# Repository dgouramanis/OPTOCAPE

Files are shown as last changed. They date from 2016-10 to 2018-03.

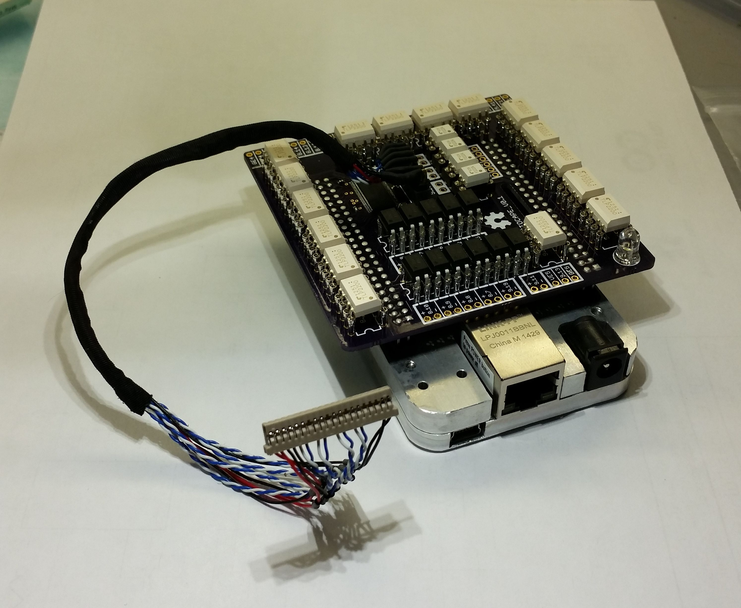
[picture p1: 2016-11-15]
hardware/images/optocape_lvds_cable.jpeg

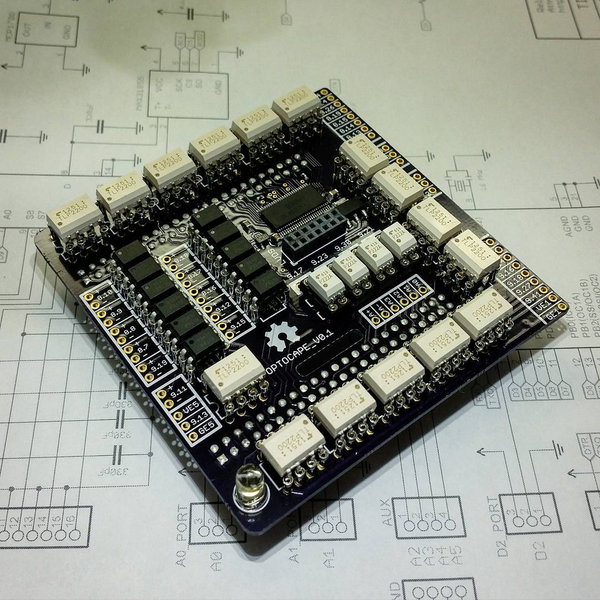
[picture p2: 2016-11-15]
hardware/images/optocape_top.png

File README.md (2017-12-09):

Photocoupler cape for BeagleBone Black with integrated video serializer

https://youtu.be/7uQYPXgA6WU

This cape was originally designed for a CNC milling machine. The opto-I/O was designed to accomidate four stepper axis with limit switches, spindle, coolant, LED light, and more. 

The UI section of the cape includes a LVDS serializer compatible with many flatscreen LCDs. Four-wire touchscreen is supported.

Features:

    15 high-speed outputs (opto)
    10 high-speed inputs (opto)
    UART TX RX (opto)    
    4 opto relay outputs (500mA)
    12 bit color LVDS video (CMOS)
    4 analog inputs (CMOS)

The outputs are divided into five sections. Each section is powered through seperate V and GND nets. 

The input voltage range is 3-6 volts.

5 VDC power source connected to DC power Jack or VDD_5V is required for LVDS.

You can buy an Optocape at the link below. 

https://www.tindie.com/products/TEMProducts/optocape/

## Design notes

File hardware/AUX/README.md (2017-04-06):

This auxiliary circuit is for connection of a mechanical switch panl user interface via UART4. Not yet tested.

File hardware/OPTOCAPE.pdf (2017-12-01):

TEM Products | Optocape

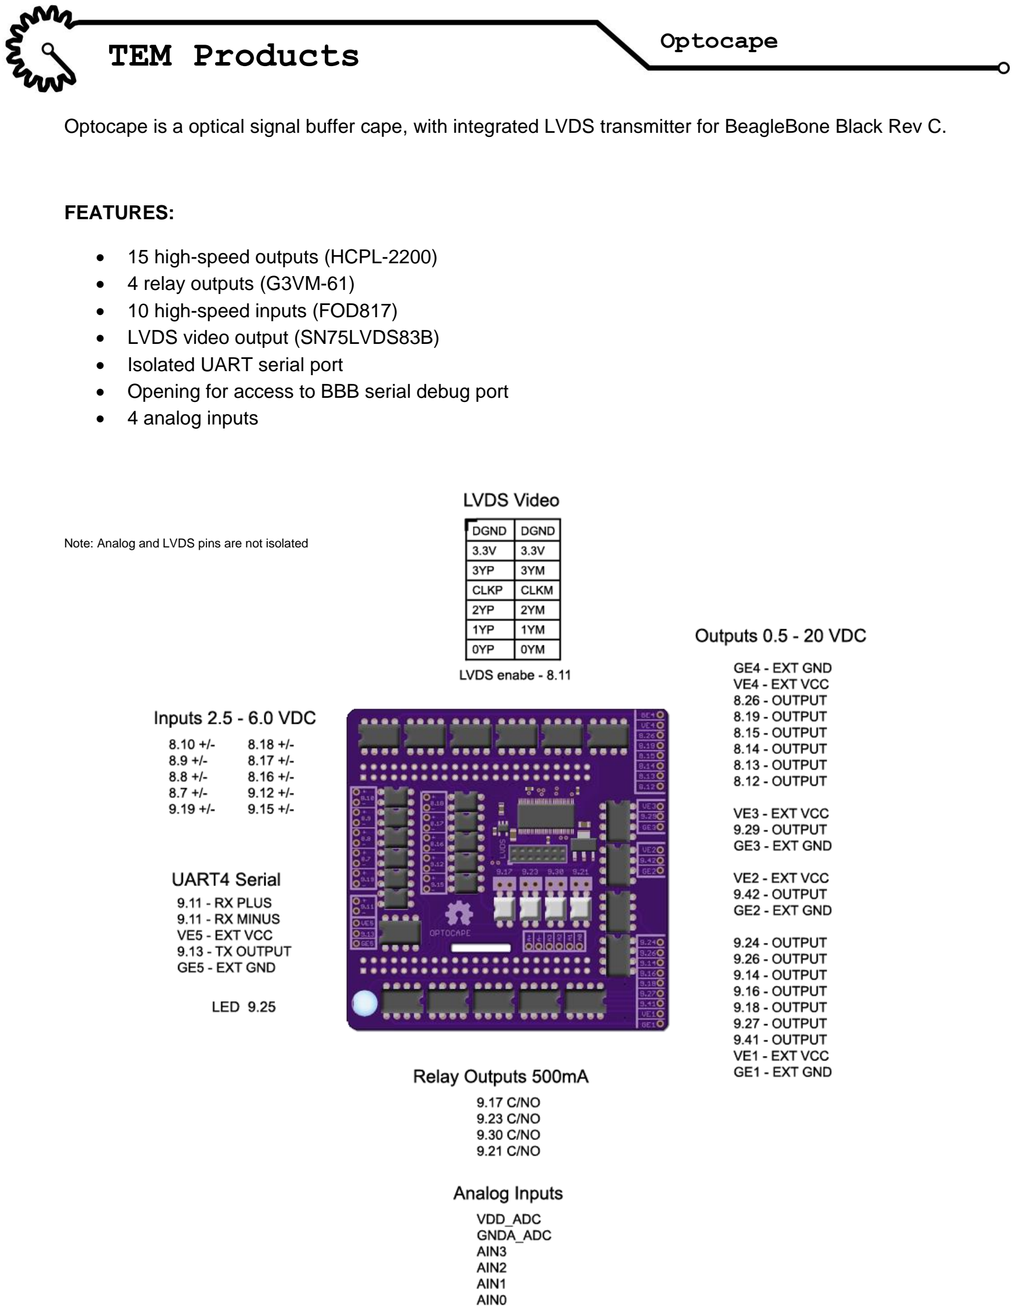
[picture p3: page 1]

Optocape is a optical signal buffer cape, with integrated LVDS transmitter for BeagleBone Black Rev C.

FEATURES:

- 15 high-speed outputs (HCPL-2200)
- 4 relay outputs (G3VM-61)
- 10 high-speed inputs (FOD817)
- LVDS video output (SN75LVDS83B)
- Isolated UART serial port
- Opening for access to BBB serial debug port
- 4 analog inputs

Note: Analog and LVDS pins are not isolated

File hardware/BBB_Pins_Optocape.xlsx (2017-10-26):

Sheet: P8
Optocape I/O | Pin | ZCZ Ball | Name | DT Offset | Mode
 |  |  |  |  | 0 | 1 | 2 | 3 | 4 | 5 | 6 | 7
 | 1 | - | GND
 | 2 | - | GND
 | 3 | R9 | GPIO1_6 | 0x018 | gpmc_ad6 | mmc1_dat6 | - | - | - | - | - | gpio1[6]
 | 4 | T9 | GPIO1_7 | 0x01C | gpmc_ad7 | mmc1_dat7 | - | - | - | - | - | gpio1[7]
 | 5 | R8 | GPIO1_2 | 0x008 | gpmc_ad2 | mmc1_dat2 | - | - | - | - | - | gpio1[2]
 | 6 | T8 | GPIO1_3 | 0x00C | gpmc_ad3 | mmc1_dat3 | - | - | - | - | - | gpio1[3]
I | 7 | R7 | TIMER4 | 0x090 | gpmc_advn_ale | - | timer4 | - | - | - | - | gpio2[2]
I | 8 | T7 | TIMER7 | 0x094 | gpmc_oen_ren | - | timer7 | - | - | - | - | gpio2[3]
I | 9 | T6 | TIMER5 | 0x09C | gpmc_ben0_cle | - | timer5 | - | - | - | - | gpio2[5]
I | 10 | U6 | TIMER6 | 0x098 | gpmc_wen | - | timer6 | - | - | - | - | gpio2[4]
LVDS ena | 11 | R12 | GPIO1_13 | 0x034 | gpmc_ad13 | lcd_data18 | mmc1_dat5 | mmc2_dat1 | eQEP2B_in | pr1_mii0_txd1 | pr1_pru0_pru_r30_15 | gpio1[13]
O | 12 | T12 | GPIO1_12 | 0x030 | gpmc_ad12 | lcd_data19 | mmc1_dat4 | mmc2_dat0 | eQEP2A_IN | pr1_mii0_txd2 | pr1_pru0_pru_r30_14 | gpio1[12]
O | 13 | T10 | EHRPWM2B | 0x024 | gpmc_ad9 | lcd_data22 | mmc1_dat1 | mmc2_dat5 | ehrpwm2B | pr1_mii0_col | - | gpio0[23]
O | 14 | T11 | GPIO0_26 | 0x028 | gpmc_ad10 | lcd_data21 | mmc1_dat2 | mmc2_dat6 | ehrpwm2_tripzone_in | pr1_mii0_txen | - | gpio0[26]
O | 15 | U13 | GPIO1_15 | 0x03C | gpmc_ad15 | lcd_data16 | mmc1_dat7 | mmc2_dat3 | eQEP2_strobe | pr1_ecap0_ecap_capin_apwm_o | pr1_pru0_pru_r31_15 | gpio1[15]
I | 16 | V13 | GPIO1_14 | 0x038 | gpmc_ad14 | lcd_data17 | mmc1_dat6 | mmc2_dat2 | eQEP2_index | pr1_mii0_txd0 | pr1_pru0_pru_r31_14 | gpio1[14]
I | 17 | U12 | GPIO0_27 | 0x02C | gpmc_ad11 | lcd_data20 | mmc1_dat3 | mmc2_dat7 | ehrpwm0_synco | pr1_mii0_txd3 | - | gpio0[27]
I | 18 | V12 | GPIO2_1 | 0x08C | gpmc_clk | lcd_memory_clk | gpmc_wait1 | mmc2_clk | pr1_mii1_crs | pr1_mdio_mdclk | mcasp0_fsr | gpio2[1]
O | 19 | U10 | EHRPWM2A | 0x020 | gpmc_ad8 | lcd_data23 | mmc1_dat0 | mmc2_dat4 | ehrpwm2A | pr1_mii_mt0_clk | - | gpio0[22]
 | 20 | V9 | GPIO1_31 | 0x084 | gpmc_csn2 | gpmc_be1n | mmc1_cmd | pr1_edio_data_in7 | pr1_edio_data_out7 | pr1_pru1_pru_r30_13 | pr1_pru1_pru_r31_13 | gpio1[31]
 | 21 | U9 | GPIO1_30 | 0x080 | gpmc_csn1 | gpmc_clk | mmc1_clk | pr1_edio_data_in6 | pr1_edio_data_out6 | pr1_pru1_pru_r30_12 | pr1_pru1_pru_r31_12 | gpio1[30] | Output
 | 22 | V8 | GPIO1_5 | 0x014 | gpmc_ad5 | mmc1_dat5 | - | - | - | - | - | gpio1[5] | Input
 | 23 | U8 | GPIO1_4 | 0x010 | gpmc_ad4 | mmc1_dat4 | - | - | - | - | - | gpio1[4] | I/O
 | 24 | V7 | GPIO1_1 | 0x004 | gpmc_ad1 | mmc1_dat1 | - | - | - | - | - | gpio1[1]
 | 25 | U7 | GPIO1_0 | 0x000 | gpmc_ad0 | mmc1_dat0 | - | - | - | - | - | gpio1[0]
O | 26 | V6 | GPIO1_29 | 0x07C | gpmc_csn0 | - | - | - | - | - | - | gpio1[29]
 | 27 | U5 | GPIO2_22 | 0x0E0 | lcd_vsync | gpmc_a8 | gpmc_a1 | pr1_edio_data_in2 | pr1_edio_data_out2 | pr1_pru1_pru_r30_8 | pr1_pru1_pru_r31_8 | gpio2[22]
 | 28 | V5 | GPIO2_24 | 0x0E8 | lcd_pclk | gpmc_a10 | pr1_mii0_crs | pr1_edio_data_in4 | pr1_edio_data_out4 | pr1_pru1_pru_r30_10 | pr1_pru1_pru_r31_10 | gpio2[24]
 | 29 | R5 | GPIO2_23 | 0x0E4 | lcd_hsync | gpmc_a9 | gpmc_a2 | pr1_edio_data_in3 | pr1_edio_data_out3 | pr1_pru1_pru_r30_9 | pr1_pru1_pru_r31_9 | gpio2[23]
 | 30 | R6 | GPIO2_25 | 0x0EC | lcd_ac_bias_en | gpmc_a11 | pr1_mii1_crs | pr1_edio_data_in5 | pr1_edio_data_out5 | pr1_pru1_pru_r30_11 | pr1_pru1_pru_r31_11 | gpio2[25]
 | 31 | V4 | UART5_CTSN | 0x0D8 | lcd_data14 | gpmc_a18 | eQEP1_index | mcasp0_axr1 | uart5_rxd | pr1_mii0_rxd3 | uart5_ctsn | gpio0[10]
 | 32 | T5 | UART5_RTSN | 0x0DC | lcd_data15 | gpmc_a19 | eQEP1_strobe | mcasp0_ahclkx | mcasp0_axr3 | pr1_mii0_rxdv | uart5_rtsn | gpio0[11]
 | 33 | V3 | UART4_RTSN | 0x0D4 | lcd_data13 | gpmc_a17 | eQEP1B_in | mcasp0_fsr | mcasp0_axr3 | pr1_mii0_rxer | uart4_rtsn | gpio0[9]
 | 34 | U4 | UART3_RTSN | 0x0CC | lcd_data11 | gpmc_a15 | ehrpwm1B | mcasp0_ahclkr | mcasp0_axr2 | pr1_mii0_rxd0 | uart3_rtsn | gpio2[17]
 | 35 | V2 | UART4_CTSN | 0x0D0 | lcd_data12 | gpmc_a16 | eQEP1A_in | mcasp0_aclkr | mcasp0_axr2 | pr1_mii0_rxlink | uart4_ctsn | gpio0[8]
 | 36 | U3 | UART3_CTSN | 0x0C8 | lcd_data10 | gpmc_a14 | ehrpwm1A | mcasp0_axr0 | - | pr1_mii0_rxd1 | uart3_ctsn | gpio2[16]
 | 37 | U1 | UART5_TXD | 0x0C0 | lcd_data8 | gpmc_a12 | ehrpwm1_tripzone_in | mcasp0_aclkx | uart5_txd | pr1_mii0_rxd3 | uart2_ctsn | gpio2[14]
 | 38 | U2 | UART5_RXD | 0x0C4 | lcd_data9 | gpmc_a13 | ehrpwm0_synco | mcasp0_fsx | uart5_rxd | pr1_mii0_rxd2 | uart2_rtsn | gpio2[15]
 | 39 | T3 | GPIO2_12 | 0x0B8 | lcd_data6 | gpmc_a6 | pr1_edio_data_in6 | eQEP2_index | pr1_edio_data_out6 | pr1_pru1_pru_r30_6 | pr1_pru1_pru_r31_6 | gpio2[12]
 | 40 | T4 | GPIO2_13 | 0x0BC | lcd_data7 | gpmc_a7 | pr1_edio_data_in7 | eQEP2_strobe | pr1_edio_data_out7 | pr1_pru1_pru_r30_7 | pr1_pru1_pru_r31_7 | gpio2[13]
 | 41 | T1 | GPIO2_10 | 0x0B0 | lcd_data4 | gpmc_a4 | pr1_mii0_txd1 | eQEP2A_in | - | pr1_pru1_pru_r30_4 | pr1_pru1_pru_r31_4 | gpio2[10]
 | 42 | T2 | GPIO2_11 | 0x0B4 | lcd_data5 | gpmc_a5 | pr1_mii0_txd0 | eQEP2B_in | - | pr1_pru1_pru_r30_5 | pr1_pru1_pru_r31_5 | gpio2[11]
 | 43 | R3 | GPIO2_8 | 0x0A8 | lcd_data2 | gpmc_a2 | pr1_mii0_txd3 | ehrpwm2_tripzone_in | - | pr1_pru1_pru_r30_2 | pr1_pru1_pru_r31_2 | gpio2[8]
 | 44 | R4 | GPIO2_9 | 0x0AC | lcd_data3 | gpmc_a3 | pr1_mii0_txd2 | ehrpwm0_synco | - | pr1_pru1_pru_r30_3 | pr1_pru1_pru_r31_3 | gpio2[9]
 | 45 | R1 | GPIO2_6 | 0x0A0 | lcd_data0 | gpmc_a0 | pr1_mii_mt0_clk | ehrpwm2A | - | pr1_pru1_pru_r30_0 | pr1_pru1_pru_r31_0 | gpio2[6]
 | 46 | R2 | GPIO2_7 | 0x0A4 | lcd_data1 | gpmc_a1 | pr1_mii0_txen | ehrpwm2B | - | pr1_pru1_pru_r30_1 | pr1_pru1_pru_r31_1 | gpio2[7]

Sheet: P9
Optocape I/O | Pin | ZCZ Ball | Name | DT Offset | Mode
 |  |  |  |  | 0 | 1 | 2 | 3 | 4 | 5 | 6 | 7
 | 1 | - | GND
 | 2 | - | GND
 | 3 | - | DC_3.3V
 | 4 | - | DC_3.3V
 | 5 | - | VDD_5V
 | 6 | - | VDD_5V
 | 7 | - | SYS_5V
 | 8 | - | SYS_5V
 | 9 | - | PWR_BUT
 | 10 | A10 | SYS_RESETn |  | RESET_OUT | - | - | - | - | - | - | -
I | 11 | T17 | UART4_RXD | 0x070 | gpmc_wait0 | mii2_crs | gpmc_csn4 | rmii2_crs_dv | mmc1_sdcd | pr1_mii1_col | uart4_rxd | gpio0[30]
I | 12 | U18 | GPIO1_28 | 0x078 | gpmc_ben1 | mii2_col | gpmc_csn6 | mmc2_dat3 | gpmc_dir | pr1_mii1_rxlink | mcasp0_aclkr | gpio1[28]
O | 13 | U17 | UART4_TXD | 0x074 | gpmc_wpn | mii2_rxerr | gpmc_csn5 | rmii2_rxerr | mmc2_sdcd | pr1_mii1_txen | uart4_txd | gpio0[31]
O | 14 | U14 | EHRPWM1A | 0x048 | gpmc_a2 | mii2_txd3 | rgmii2_td3 | mmc2_dat1 | gpmc_a18 | pr1_mii1_txd2 | ehrpwm1A | gpio1[18]
I | 15 | R13 | GPIO1_16 | 0x040 | gpmc_a0 | gmii2_txen | rmii2_tctl | mii2_txen | gpmc_a16 | pr1_mii_mt1_clk | ehrpwm1_tripzone_input | gpio1[16]
O | 16 | T14 | EHRPWM1B | 0x04C | gpmc_a3 | mii2_txd2 | rgmii2_td2 | mmc2_dat2 | gpmc_a19 | pr1_mii1_txd1 | ehrpwm1B | gpio1[19]
Relay | 17 | A16 | I2C1_SCL | 0x15C | spi0_cs0 | mmc2_sdwp | I2C1_SCL | ehrpwm0_synci | pr1_uart0_txd | pr1_edio_data_in1 | pr1_edio_data_out1 | gpio0[5]
O | 18 | B16 | I2C1_SDA | 0x158 | spi0_d1 | mmc1_sdwp | I2C1_SDA | ehrpwm0_tripzone | pr1_uart0_rxd | pr1_edio_data_in0 | pr1_edio_data_out0 | gpio0[4]
I | 19 | D17 | I2C2_SCL | 0x17C | uart1_rtsn | timer5 | dcan0_rx | I2C2_SCL | spi1_cs1 | pr1_uart0_rts_n | pr1_edc_latch1_in | gpio0[13]
 | 20 | D18 | I2C2_SDA | 0x178 | uart1_ctsn | timer6 | dcan0_tx | I2C2_SDA | spi1_cs0 | pr1_uart0_cts_n | pr1_edc_latch0_in | gpio0[12]
Relay | 21 | B17 | UART2_TXD | 0x154 | spi0_d0 | uart2_txd | I2C2_SCL | ehrpwm0B | pr1_uart0_rts_n | pr1_edio_latch_in | EMU3 | gpio0[3]
 | 22 | A17 | UART2_RXD | 0x150 | spi0_sclk | uart2_rxd | I2C2_SDA | ehrpwm0A | pr1_uart0_cts_n | pr1_edio_sof | EMU2 | gpio0[2] | Output
Relay | 23 | V14 | GPIO1_17 | 0x044 | gpmc_a1 | gmii2_rxdv | rgmii2_rxdv | mmc2_dat0 | gpmc_a17 | pr1_mii1_txd3 | ehrpwm0_synco | gpio1[17] | Input
O | 24 | D15 | UART1_TXD | 0x184 | uart1_txd | mmc2_sdwp | dcan1_rx | I2C1_SCL | - | pr1_uart0_txd | pr1_pru0_pru_r31_16 | gpio0[15] | I/O
LED | 25 | A14 | GPIO3_21 | 0x1AC | mcasp0_ahclkx | eQEP0_strobe | mcasp0_axr3 | mcasp1_axr1 | EMU4 | pr1_pru0_pru_r30_7 | pr1_pru0_pru_r31_7 | gpio3[21]
O | 26 | D16 | UART1_RXD | 0x180 | uart1_rxd | mmc1_sdwp | dcan1_tx | I2C1_SDA | - | pr1_uart0_rxd | pr1_pru1_pru_r31_16 | gpio0[14]
O | 27 | C13 | GPIO3_19 | 0x1A4 | mcasp0_fsr | eQEP0B_in | mcasp0_axr3 | mcasp1_fsx | EMU2 | pr1_pru0_pru_r30_5 | pr1_pru0_pru_r31_5 | gpio3[19]
 | 28 | C12 | SPI1_CS0 | 0x19C | mcasp0_ahclkr | ehrpwm0_synci | mcasp0_axr2 | spi1_cs0 | eCAP2_in_PWM2_out | pr1_pru0_pru_r30_3 | pr1_pru0_pru_r31_3 | gpio3[17]
O | 29 | B13 | SPI1_D0 | 0x194 | mcasp0_fsx | ehrpwm0B | - | spi1_d0 | mmc1_sdcd | pr1_pru0_pru_r30_1 | pr1_pru0_pru_r31_1 | gpio3[15]
Relay | 30 | D12 | SPI1_D1 | 0x198 | mcasp0_axr0 | ehrpwm0_tripzone | - | spi1_d1 | mmc2_sdcd | pr1_pru0_pru_r30_2 | pr1_pru0_pru_r31_2 | gpio3[16]
 | 31 | A13 | SPI1_SCLK | 0x190 | mcasp0_aclkx | ehrpwm0A | - | spi1_sclk | mmc0_sdcd | pr1_pru0_pru_r30_0 | pr1_pru0_pru_r31_0 | gpio3[14]
 | 32 | - | VADC
 | 33 | C8 | AIN4
 | 34 | - | AGND
 | 35 | A8 | AIN6
 | 36 | B8 | AIN5
 | 37 | B7 | AIN2
 | 38 | A7 | AIN3
 | 39 | B6 | AIN0
 | 40 | C7 | AIN1
O | 41 | D14 | CLKOUT2 | 0x1B4 | xdma_event_intr1 | - | tclkin | clkout2 | timer7 | pr1_pru0_pru_r31_16 | EMU3 | gpio0[20]
 | # | D13 | GPIO3_20 | 0x1A8 | mcasp0_axr1 | eQEP0_index | - | Mcasp1_axr0 | EMU3 | pr1_pru0_pru_r30_6 | pr1_pru0_pru_r31_6 | gpio3[20]
O | 42 | C18 | GPIO0_7 | 0x164 | eCAP0_in_PWM0_out | uart3_txd | spi1_cs1 | pr1_ecap0_ecap_capin_apwm_o | spi1_sclk | mmc0_sdwp | xdma_event_intr2 | gpio0[7]
 | @ | B12 | GPIO3_18 | 0x1A0 | mcasp0_aclkr | eQEP0A_in | mcaspo_axr2 | mcasp1_aclkx | mmc0_sdwp | pr1_pru0_pru_r30_4 | pr1_pru0_pru_r31_4 | gpio3[18]
 | 43 | - | GND
 | 44 | - | GND
 | 45 | - | GND
 | 46 | - | GND
 |  |  | #,@ - 2 Signals available on pins 41 and 42, set the unused signal to Input

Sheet: Pin Mode Register Value
 | Slew Rate | Type | Pull up/down | Mode | Value
Modify This Line >>>> | Fast | Input | Pull Down | 0 | 0x00 | <<<< Copy & Paste This!
 | 0 | 0 | 0 | 0
Slew Rate | Fast | 0
Bit 6 | Slow | 1
Input/Output | Output | 1
Bit 5 | Input | 0
Pull Up/Down | Pull Down | 0
Bits 3-4 | Disabled | 1
 | Pull Up | 2
Mode | 0
Bits 0-2 | 1
 | 2
 | 3
 | 4
 | 5
 | 6
 | 7
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

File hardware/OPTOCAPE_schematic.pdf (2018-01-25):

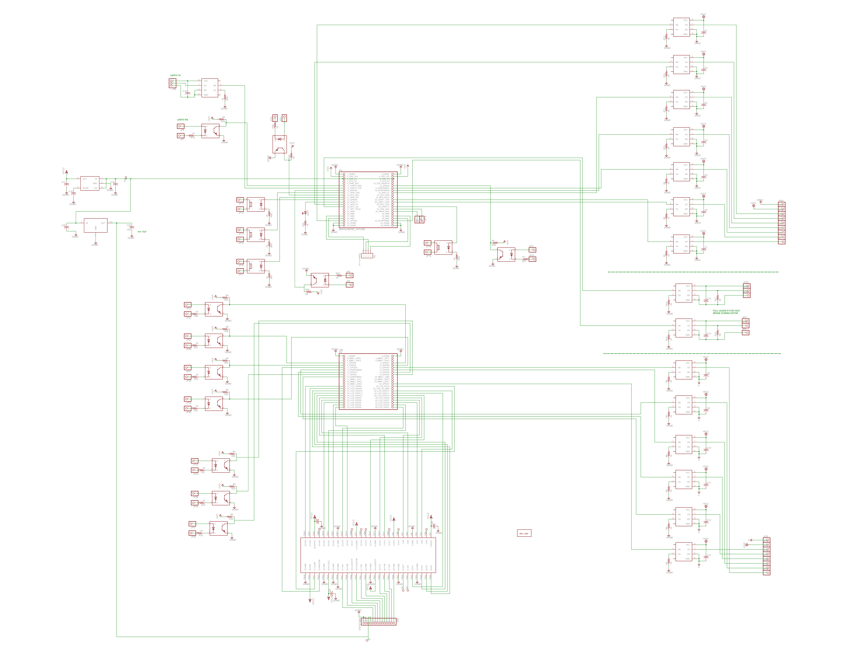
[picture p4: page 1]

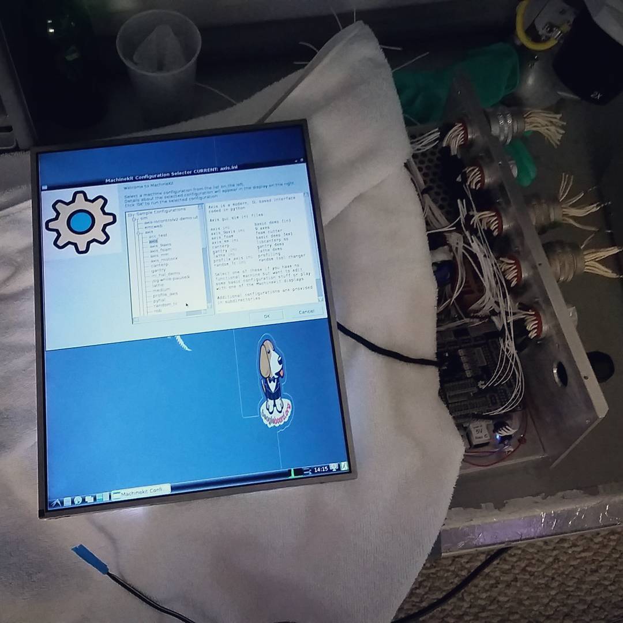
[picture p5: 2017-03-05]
hardware/images/optocape_lcd_working.jpg

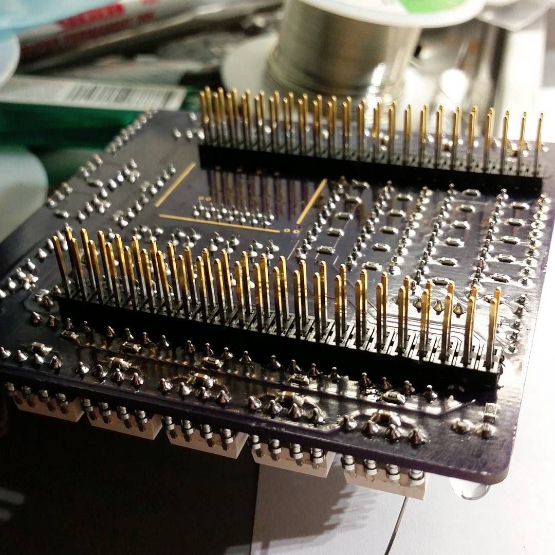
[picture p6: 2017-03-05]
hardware/images/optocape_bottom.jpg

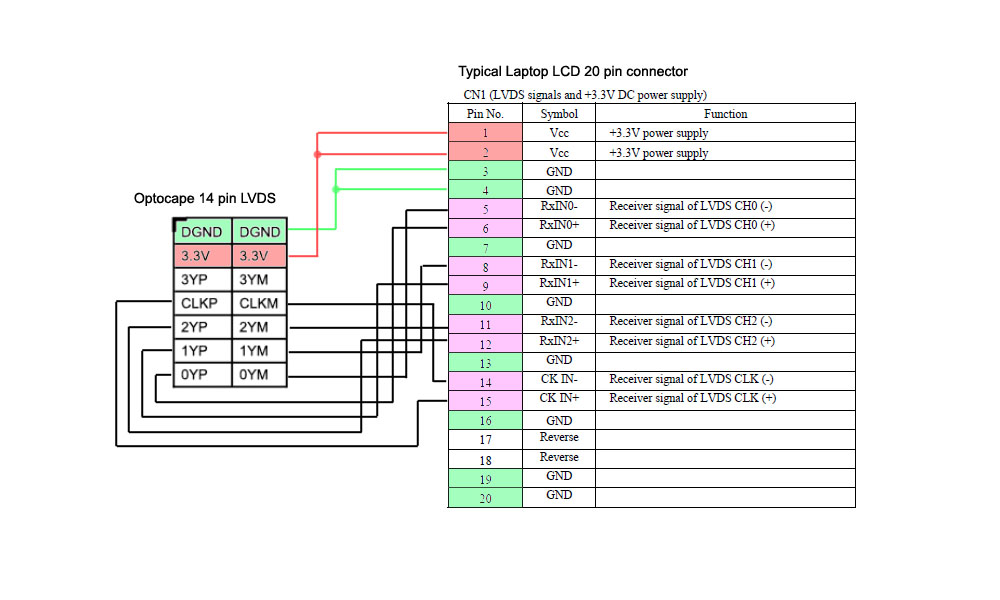
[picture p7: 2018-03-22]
hardware/TYPICAL LVDS OPTOCAPE.jpg

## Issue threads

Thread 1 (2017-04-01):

UART4 RX inverted

dgouramanis, 2017-04-01:
The Opto buffer for P9.11 inverts the incoming serial data. So an incoming start bit from external system should be HIGH.

dgouramanis, 2017-04-22:
The opto can be inverted like this:

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

Closed 2017-04-22.

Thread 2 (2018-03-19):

Touch LCD and MachineKit hints?

JetForMe, 2018-03-19:
I tried messaging on Tindie but got no reply.

Do you know if your cape will work with the 4D Systems [touch cape](https://www.4dsystems.com.au/product/gen4_4DCAPE/)?

Also, I just got MachineKit installed on my BBB, and I'm having trouble getting going. Do you have an example configuration for OPTOCAPE or any hints? Obviously I'll have to customize it for my specific I/O, but it should be able to at least pretend the cape is attached.

dgouramanis, 2018-03-19:
The 4D touch cape & Optocape would conflict. [Page 10](https://www.4dsystems.com.au/productpages/gen4-4DCAPE/downloads/gen4-4DCAPE_datasheet_R_1_0.pdf) shows connections to the headers. First, both capes are interfacing with the LCD pins. Usually that's ok, but in this case the video signals are very high speed. You're likely to get video distortions. Also P1_B pins 14-30 share many connections with Optocape. You could potentially get them working together by modifying the PCBs...

But no reason to do that. Optocape has Touch + LCD capabilities. Optocape can do Resistive touch with no external hardware. You can also do Capacitive or IR touch via USB device (kits like this are popular on eBay). My setup uses an old Sharp 14.1" laptop LCD. (Any LVDS laptop screen should work.) I was able to find a resistive touch overlay to match the size. Both the LCD and Touch sensor wire directly to Optocape.

[Here](https://github.com/dgouramanis/OPTOCAPE/blob/master/device%20tree/BB-OPTOCAPE1-00A0.dts) is a link to the .dts example. You can adjust the resolution and resistance values to fit your needs. I expect Optocape works with most used screens on eBay. "[LVDS Flatlink](http://www.ti.com/product/SN75LVDS83B)" is a standardized protocol across many laptops. Although I did try briefly with a newer Samsung screen, and haven't got it working yet. I suggest going for an older model <2010.

dgouramanis, 2018-03-19:
Last I tried Machinekit they were using a Version 3.8 kernel. I was unable to get a custom LCD working with that version. I upgraded to the latest BeagleBone [image](http://beagleboard.org/latest-images), and installed [BeagleG](https://github.com/hzeller/beagleg) instead. Works perfectly.

JetForMe, 2018-03-19:
Ah, regarding the cape LCD connection, that's a pity. I really like this touch display. It's capacitive, for one, and generally quite nice. I may end up desoldering the serializer, but I'll look at the pins used by both to be sure before I do.

I'm currently running a Stretch-based MachineKit with a 4.14 kernel. Everything seems to be working, I just don't know yet how to configure it. I'll take a look at BeagleG, too.

dgouramanis, 2018-03-19:
Won't damage anything by running both serializers connected, so it's worth a try. You can set 8.11 low to disable Optocape serializer. It may work. Worst case the picture is shaky.

Bigger problem is with GPIO pins 9.14-9.19, 9.21, 9.23, 9.26, 9.30 are conflicting.

JetForMe, 2018-03-19:
So, P9.15, 16, 21, 23, and 30 only conflict if a button board is connected to the other FPC connector. I don't need to use those.

P9.14 is the backlight PWM, connected to JP2. p9.17 (JP14 & 15), 18 (JP5), and 26 (JP1) are part of the capacitive touch sensor, so those would have to be made available. P9.19 (JP30 & 31) & 20 (unconnected on OPTOCAPE) are part of the CAPE EEPROM support.

#### Conflicting Pins
| BBB Header Pin | OPTOCAPE Function |
| :---: | :---: |
| P9.14 | JP2 |
| P9.17 | JP14 & JP15 |
| P9.18 | JP5 |
| P9.19 | JP30 & JP31 |
| P9.26 | JP1 |

So far, I think I need 6 direct PRU outputs and 12 direct inputs, plus 5 additional outputs and one additional input. I haven’t yet tried to map those to the available I/O.

JetForMe, 2018-03-20:
Hmm, the ICs aren't labeled. Could you tell me which ones (inputs) to pull, to avoid the conflicts above? I can poke at it to try to find them, but I figure you'd be able to tell me more reliably.

dgouramanis, 2018-03-20:
Here is a [diagram](https://644db4de3505c40a0444-327723bce298e3ff5813fb42baeefbaa.ssl.cf1.rackcdn.com/681a1287ef127f76477feb6b8de48beb.png).

JetForMe, 2018-03-20:
Thanks. P9.19 should be fine, I think. 10K plenty weak. I have to go out of town for a few days, and this weekend is slammed, but I'll let you know how it goes!

JetForMe, 2018-03-20:
Hmm. I pulled the ICs, plugged in both capes, but the board doesn't come up (no console output, no lights, just the main power LED on the BBB). I tried each cape individually, and it comes up fine. Something's still in conflict.

JetForMe, 2018-03-20:
A bit more info: If I disconnect the LCD/touchscreen from 30-pin FPC connector, but leave both capes stacked, it boots. Doesn't narrow it down much, but it’s less than 30 pins to check.

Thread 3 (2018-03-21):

Lvds connector

20after4, 2018-03-21:
How would I convert the 14 pin optocape lvds connector to match the connector on a laptop screen?
All of the screen's I've looked at have a high density connector. I found a bunch of cables on ebay but most of them are more than 14 pins.

dgouramanis, 2018-03-22:
I'm not an expert on LCDs. My setup uses a Sharp LQxxx TFT LCD salvaged from a Toshiba Satellite. The screen has a 20 pin LVDS connector. [Here is how it's wired up](https://github.com/dgouramanis/OPTOCAPE/blob/master/hardware/TYPICAL%20LVDS%20OPTOCAPE.jpg). It works beautifully.
As far as I know LVDS video is standardized for many laptop LCD flat panel displays. The [SN75LVDS83B](http://www.ti.com/product/SN75LVDS83B) is used on many laptop motherboards for video serilization.
To make a cable you will need a 7x2 position, 2mm pitch male header. The LCD also needs a backlight. Pin 8.11 needs to be HI to enable video. That's it for hardware. Then it's a matter of configuring firmware to output video signal. [Example here](https://github.com/dgouramanis/OPTOCAPE/blob/master/device%20tree/BB-OPTOCAPE1-00A0.dts).
If you get a screen working please post details about pinout & dts file. Hopefully we can build a knowledge base of screen pinouts & dts files. There are so many big, beautiful screens being trashed these days. Older laptops have the best screens for hacking.

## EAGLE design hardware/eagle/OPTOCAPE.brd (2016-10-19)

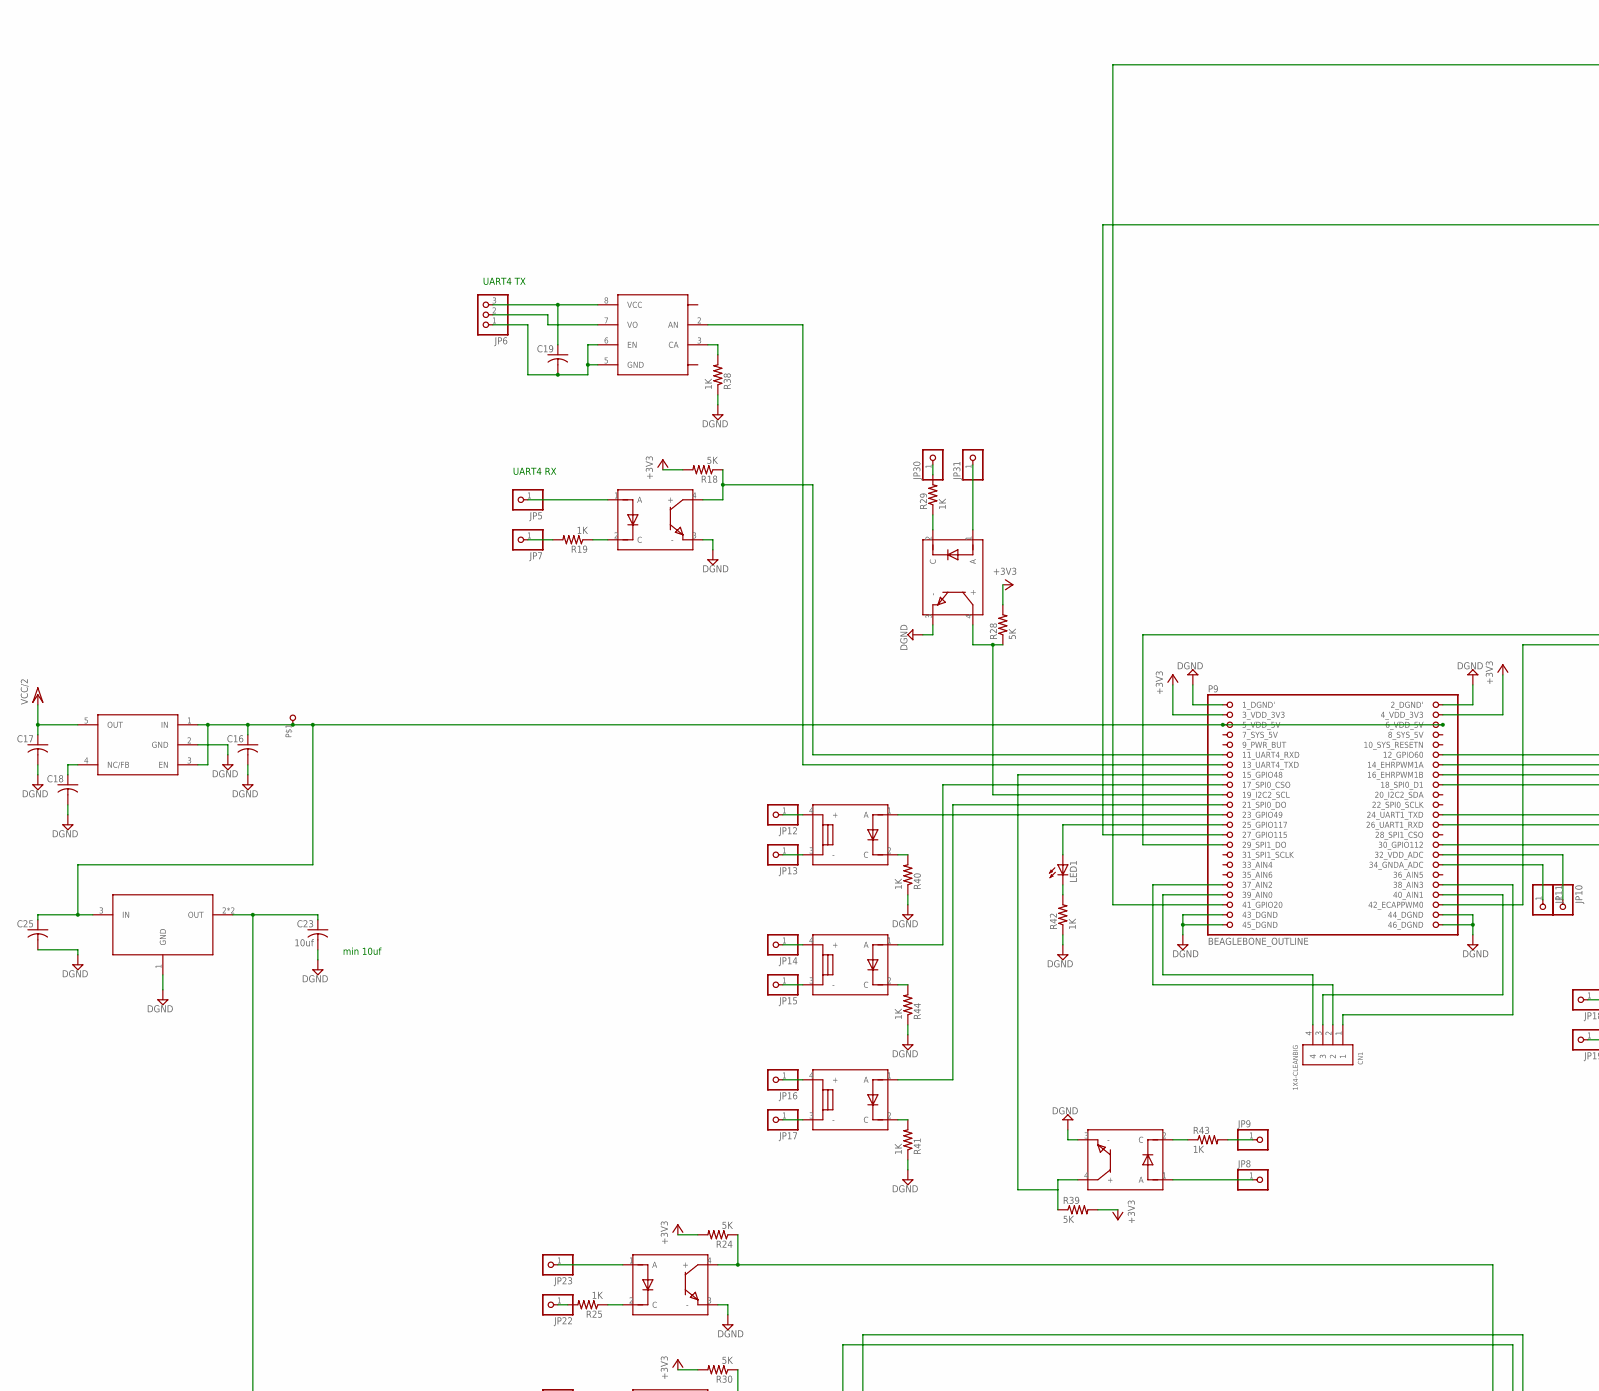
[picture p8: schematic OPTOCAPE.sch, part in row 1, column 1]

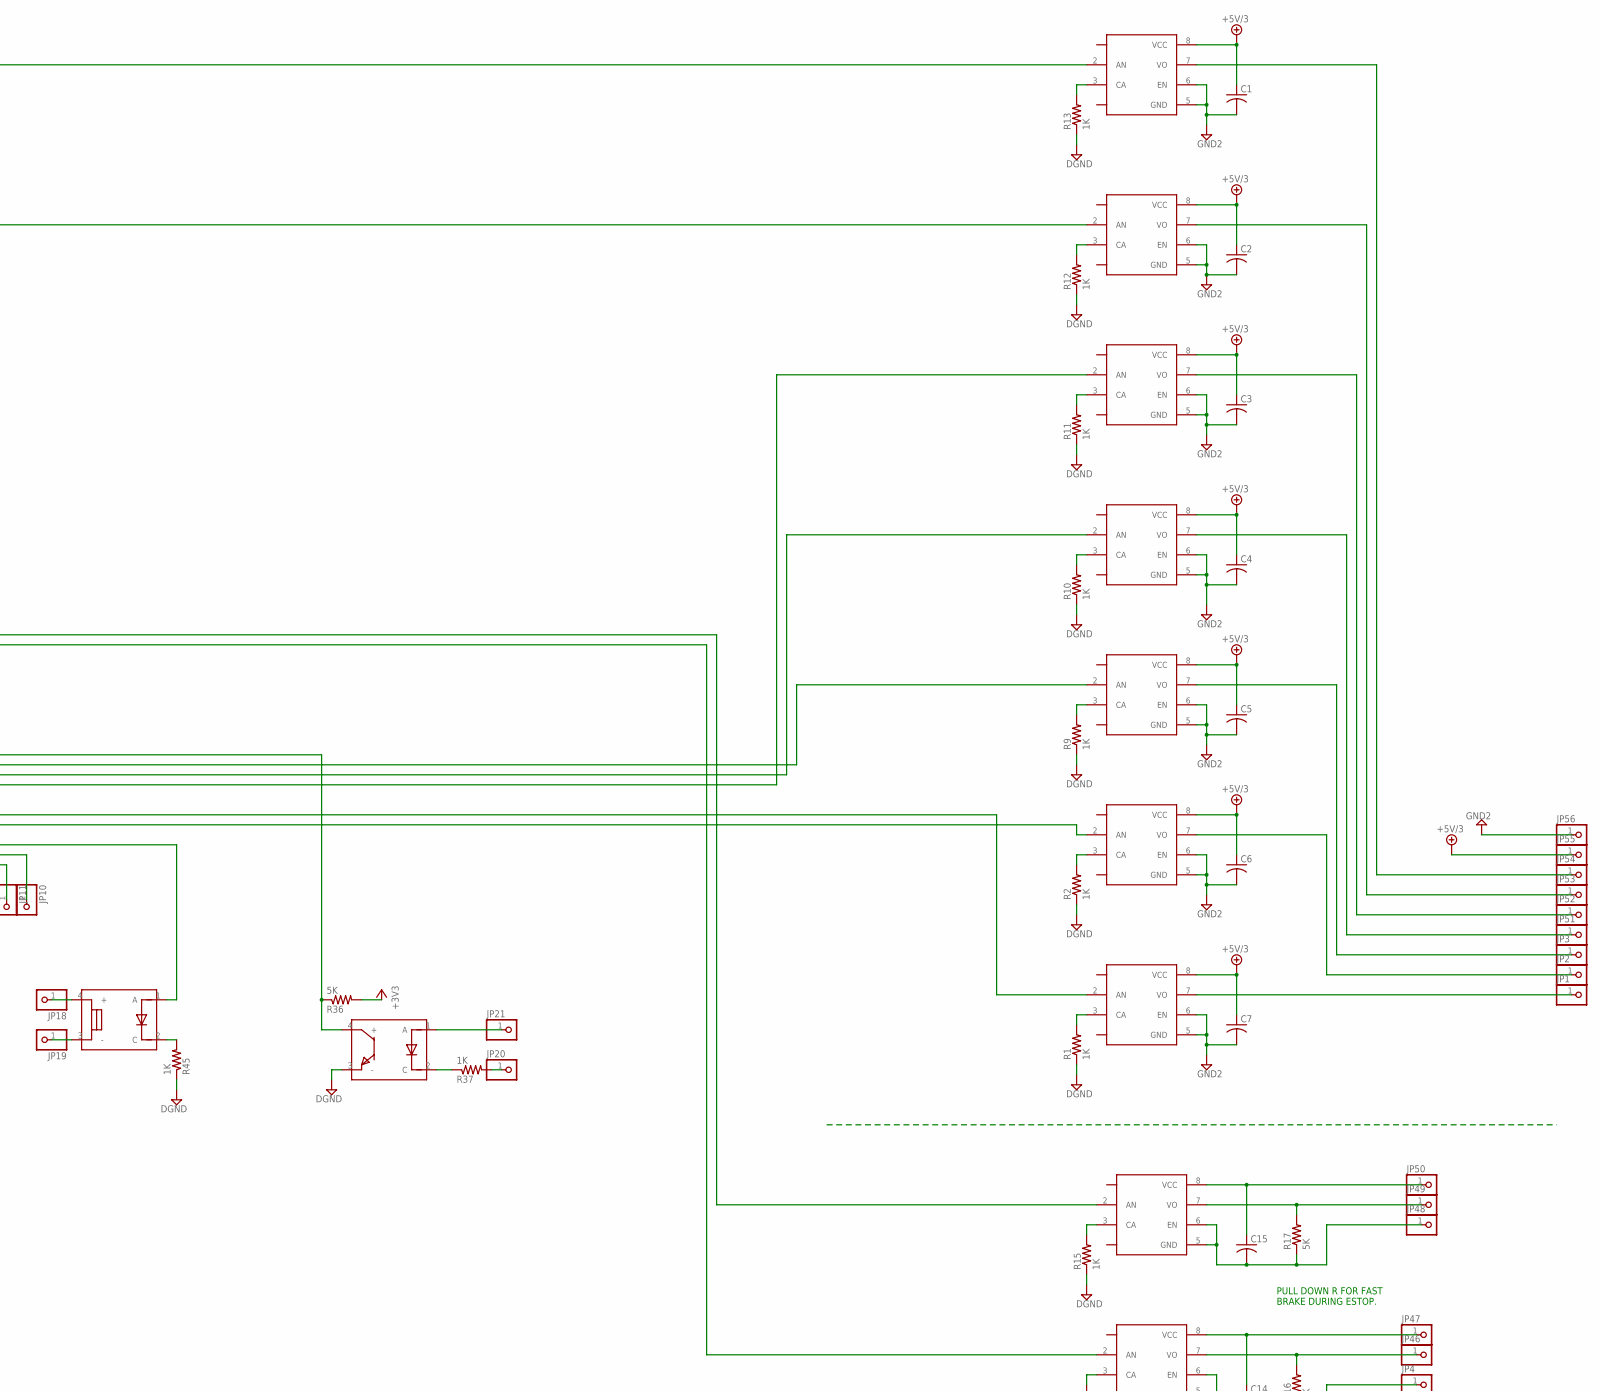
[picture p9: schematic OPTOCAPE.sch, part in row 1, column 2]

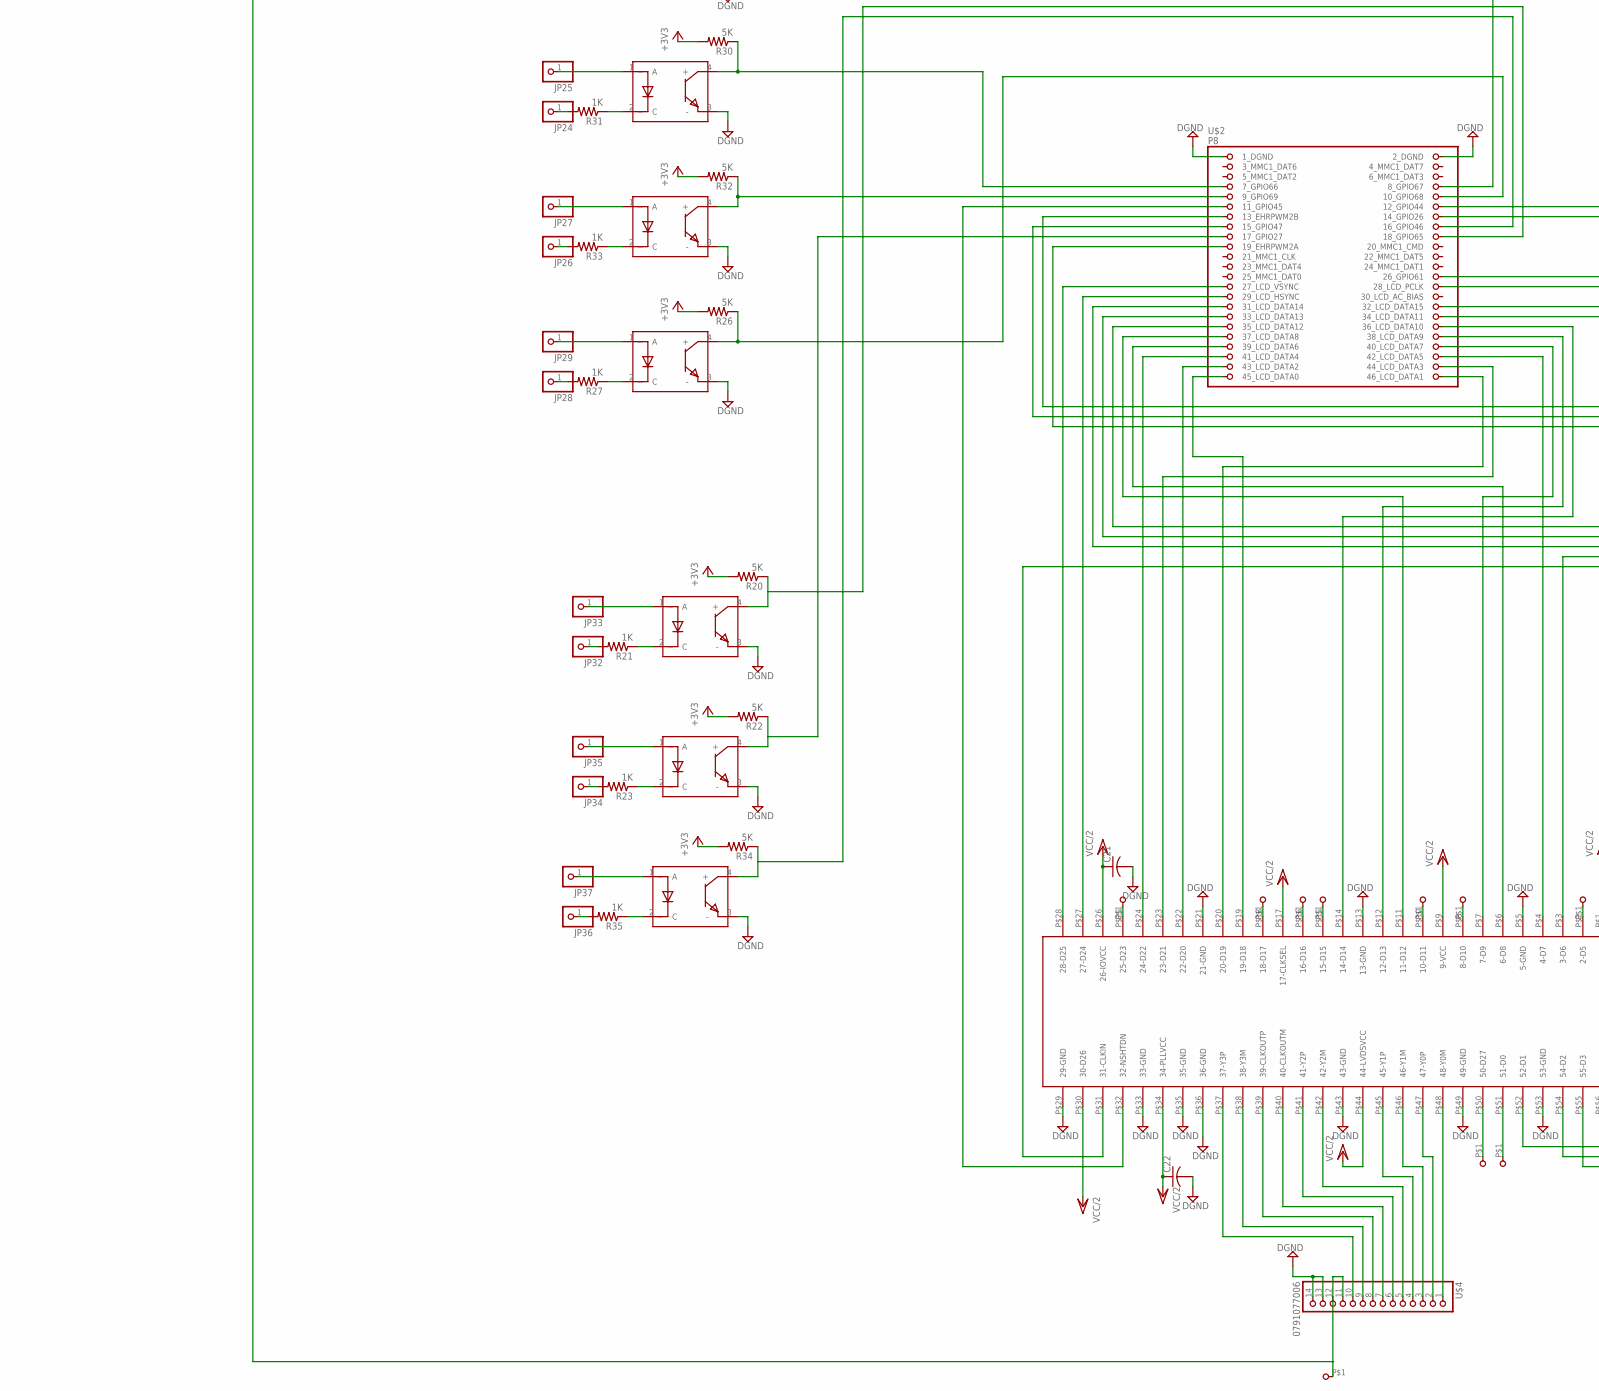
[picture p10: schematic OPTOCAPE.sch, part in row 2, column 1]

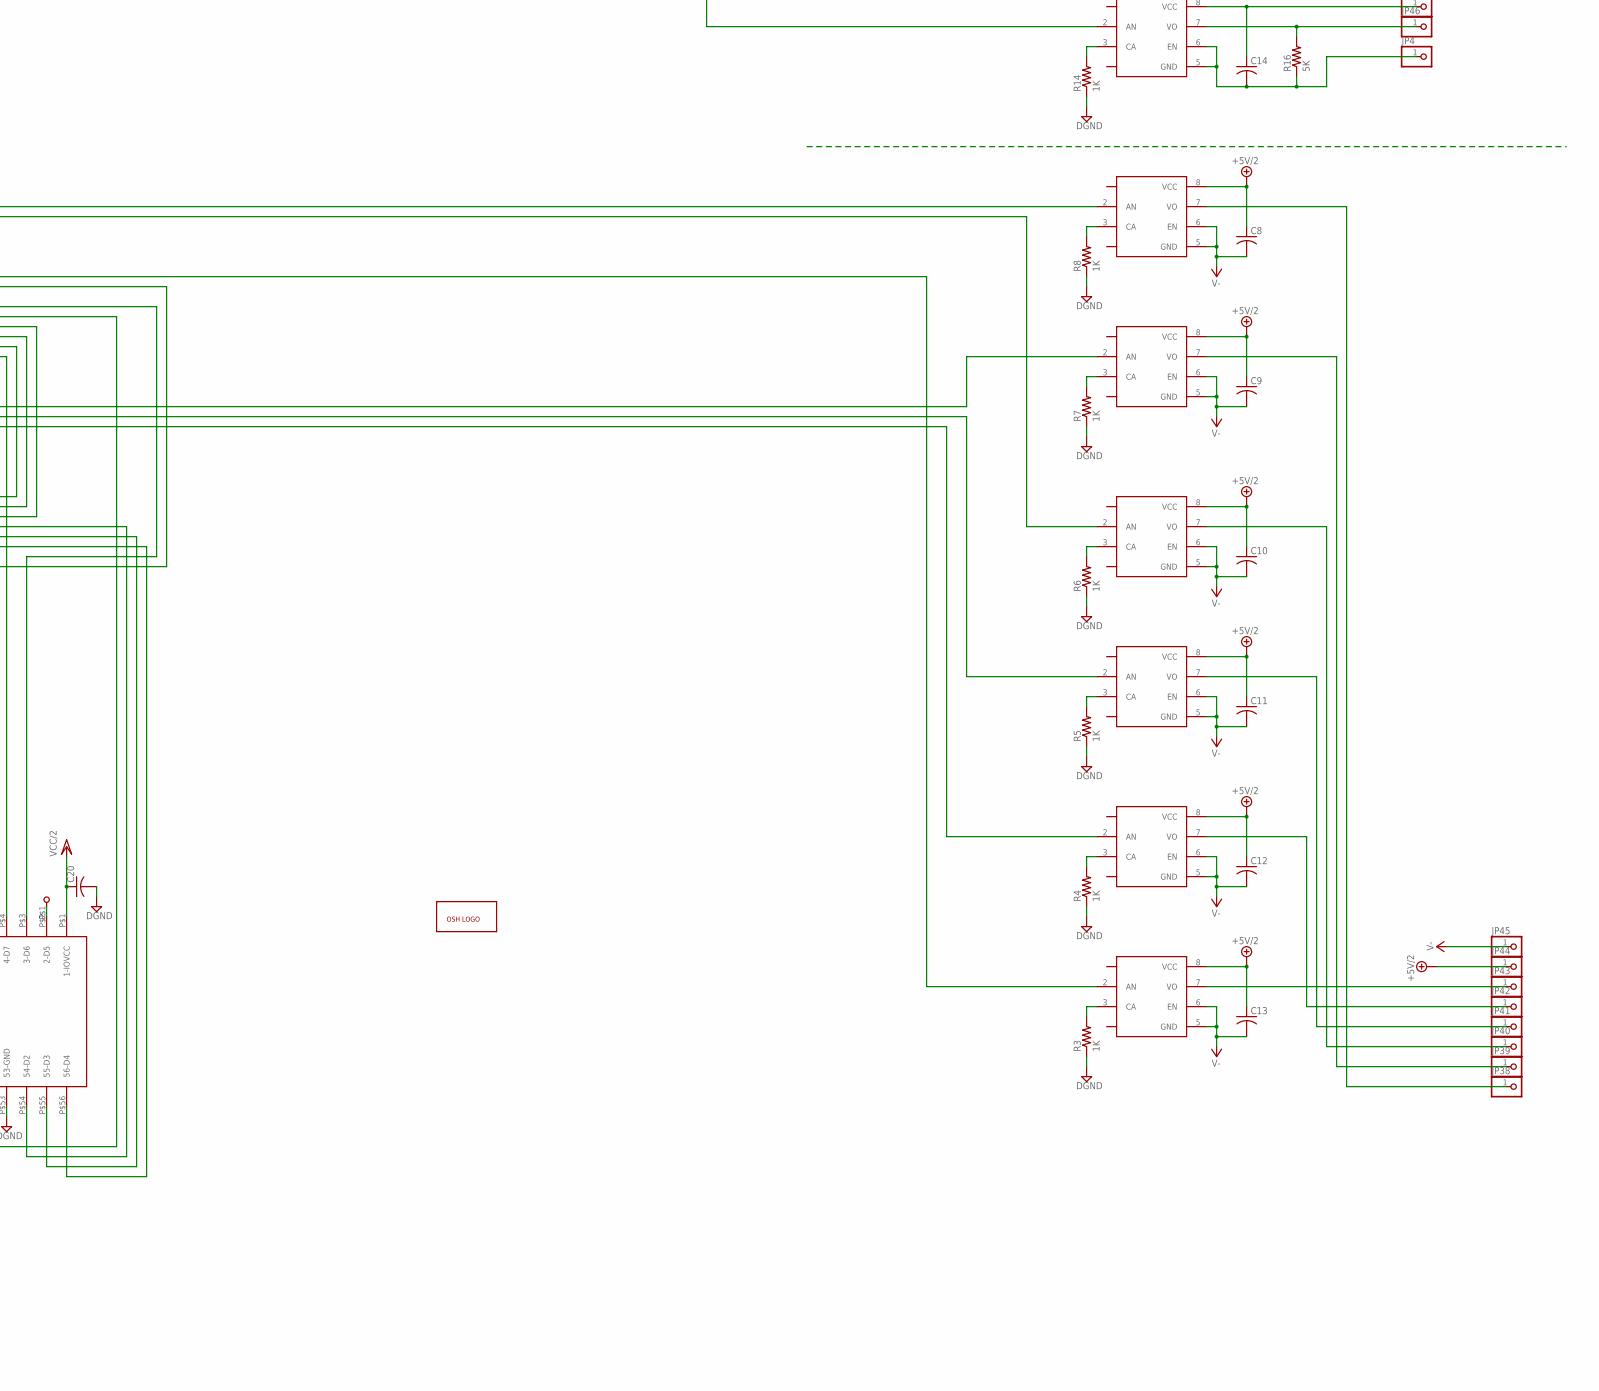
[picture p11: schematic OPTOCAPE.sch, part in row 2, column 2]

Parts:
0000, 8.12, 8.13, 8.14, 8.15, 8.19, 8.26, 9.3, 9.14, 9.16, 9.18, 9.24, 9.26, 9.27, 9.41, 1111: TLP2200F; DIL08-ROUND
C1, C2, C3, C4, C5, C6, C7, C8, C9, C10, C11, C12, C13, C14, C15, C16, C17, C19: C-USC0805K; C0805K
C18, C20, C21, C22, C25: C-USC0402; C0402
C23: 10uf; C0805K
CN1: 1X4-CLEANBIG; 1X04-CLEANBIG
JP1, JP2, JP3, JP4, JP5, JP7, JP8, JP9, JP10, JP11, JP12, JP13, JP14, JP15, JP16, JP17, JP18, JP19, JP20, JP21, JP22, JP23, JP24, JP25, JP26, JP27, JP28, JP29, JP30, JP31, JP32, JP33, JP34, JP35, JP36, JP37, JP38, JP39, JP40, JP41, JP42, JP43, JP44, JP45, JP46, JP47, JP48, JP49, JP50, JP51, JP52, JP53, JP54, JP55, JP56: PINHD-1X1CB; 1X01-CLEANBIG
JP6: PINHD-1X3CB; 1X03-CLEANBIG
LED1: LED5MM
R1, R2, R3, R4, R5, R6, R7, R8, R9, R10, R11, R12, R13, R14, R15, R19, R21, R23, R25, R27, R29, R31, R33, R35, R37, R38, R40, R41, R42, R43, R44, R45: 1K; R0603
R16, R17, R18, R20, R22, R24, R26, R28, R30, R32, R34, R36, R39: 5K; R0603
SPICS1, SPICS2, SPICS3, SPICS4: TLP222A; DIL04-ROUND
TPS73133: TPS76350DBVR; SOT23-5L
U$1, U$6, U$7, U$8, U$9, U$10, U$11, U$12, U$13, U$14, U$15: FOD817B; DIL04-ROUND
U$2: BEAGLEBONE_OUTLINE; BEAGLEBONE_SHIELD
U$3: SN75LVDS83B; DGG0056A
U$4: 0791077006
U$5, U$16, U$19, U$20, U$21, U$22, U$23, U$24, U$25, U$32, U$33: DEAN_SMALL_VIA
U$17: OSH_LOGO
U$18: LM1117; SOT223

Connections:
7_SYS_5V: U$2.53 (7_SYS_5V)
8.7: R30.1, U$2.7 (7_GPIO66), U$12.4 (+)
8.8: R24.1, U$2.8 (8_GPIO67), U$9.4 (+)
8.9: R32.1, U$2.9 (9_GPIO69), U$13.4 (+)
8.10: R26.1, U$2.10 (10_GPIO68), U$10.4 (+)
8.11: U$2.11 (11_GPIO45), U$3.P$32 (32-NSHTDN)
8.12: 8.12.2 (AN), U$2.12 (12_GPIO44)
8.13: 8.13.2 (AN), U$2.13 (13_EHRPWM2B)
8.14: 8.14.2 (AN), U$2.14 (14_GPIO26)
8.15: 8.15.2 (AN), U$2.15 (15_GPIO47)
8.16: R34.1, U$2.16 (16_GPIO46), U$14.4 (+)
8.17: R22.1, U$2.17 (17_GPIO27), U$8.4 (+)
8.18: R20.1, U$2.18 (18_GPIO65), U$7.4 (+)
8.19: 8.19.2 (AN), U$2.19 (19_EHRPWM2A)
8.26: 8.26.2 (AN), U$2.26 (26_GPIO61)
9.11: R18.1, U$2.57 (11_UART4_RXD), U$6.4 (+)
9.12: R36.1, U$2.58 (12_GPIO60), U$15.4 (+)
9.13: 9.3.2 (AN), U$2.59 (13_UART4_TXD)
9.14: 9.14.2 (AN), U$2.60 (14_EHRPWM1A)
9.15: R39.1, U$1.4 (+), U$2.61 (15_GPIO48)
9.16: 9.16.2 (AN), U$2.62 (16_EHRPWM1B)
9.17: SPICS3.1 (A), U$2.63 (17_SPI0_CSO)
9.18: 9.18.2 (AN), U$2.64 (18_SPI0_D1)
9.19: R28.1, U$2.65 (19_I2C2_SCL), U$11.4 (+)
9.21: SPICS2.1 (A), U$2.67 (21_SPI0_DO)
9.23: SPICS1.1 (A), U$2.69 (23_GPIO49)
9.24: 9.24.2 (AN), U$2.70 (24_UART1_TXD)
9.25: LED1.A, U$2.71 (25_GPIO117)
9.26: 9.26.2 (AN), U$2.72 (26_UART1_RXD)
9.27: 9.27.2 (AN), U$2.73 (27_GPIO115)
9.29: 1111.2 (AN), U$2.75 (29_SPI1_DO)
9.30: SPICS4.1 (A), U$2.76 (30_GPIO112)
9.32: JP10.1, U$2.78 (32_VDD_ADC)
9.34: JP11.1, U$2.80 (34_GNDA_ADC)
9.37: CN1.2, U$2.83 (37_AIN2)
9.38: CN1.1, U$2.84 (38_AIN3)
9.39: CN1.4, U$2.85 (39_AIN0)
9.40: CN1.3, U$2.86 (40_AIN1)
9.41: 9.41.2 (AN), U$2.87 (41_GPIO20)
9.42: 0000.2 (AN), U$2.88 (42_ECAPPWM0)
+3V3: R18.2, R20.2, R22.2, R24.2, R26.2, R28.2, R30.2, R32.2, R34.2, R36.2, R39.2, U$2.49 (3_VDD_3V3), U$2.50 (4_VDD_3V3)
+5V/2: 8.12.8 (VCC), 8.13.8 (VCC), 8.14.8 (VCC), 8.15.8 (VCC), 8.19.8 (VCC), 8.26.8 (VCC), C8.1, C9.1, C10.1, C11.1, C12.1, C13.1, JP44.1
DGND: C16.2, C17.2, C18.2, C20.2, C21.2, C22.2, C23.2, C25.2, R1.1, R2.1, R3.1, R4.1, R5.1, R6.1, R7.1, R8.1, R9.1, R10.1, R11.1, R12.1, R13.1, R14.1, R15.1, R38.1, R40.1, R41.1, R42.1, R44.1, R45.1, TPS73133.2 (GND), U$1.3 (-), U$2.1 (1_DGND), U$2.2 (2_DGND), U$2.47 (1_DGND'), U$2.48 (2_DGND'), U$2.89 (43_DGND), U$2.90 (44_DGND), U$2.91 (45_DGND), U$2.92 (46_DGND), U$3.P$5 (5-GND), U$3.P$13 (13-GND), U$3.P$21 (21-GND), U$3.P$29 (29-GND), U$3.P$33 (33-GND), U$3.P$35 (35-GND), U$3.P$36 (36-GND), U$3.P$43 (43-GND), U$3.P$49 (49-GND), U$3.P$53 (53-GND), U$4.13, U$4.14, U$6.3 (-), U$7.3 (-), U$8.3 (-), U$9.3 (-), U$10.3 (-), U$11.3 (-), U$12.3 (-), U$13.3 (-), U$14.3 (-), U$15.3 (-), U$18.1 (GND)
GND2: 9.14.5 (GND), 9.14.6 (EN), 9.16.5 (GND), 9.16.6 (EN), 9.18.5 (GND), 9.18.6 (EN), 9.24.5 (GND), 9.24.6 (EN), 9.26.5 (GND), 9.26.6 (EN), 9.27.5 (GND), 9.27.6 (EN), 9.41.5 (GND), 9.41.6 (EN), C1.2, C2.2, C3.2, C4.2, C5.2, C6.2, C7.2, JP56.1
HSYNC: U$2.29 (29_LCD_HSYNC), U$3.P$27 (27-D24)
unnamed: 9.24.3 (CA), R1.2
unnamed: C23.1, U$4.11, U$4.12, U$5.P$1, U$18.2 (OUT), U$18.TAB (OUT)
unnamed: 9.26.3 (CA), R2.2
unnamed: 8.26.3 (CA), R3.2
unnamed: 8.19.3 (CA), R4.2
unnamed: 8.15.3 (CA), R5.2
unnamed: 8.14.3 (CA), R6.2
unnamed: 8.13.3 (CA), R7.2
unnamed: 8.12.3 (CA), R8.2
unnamed: 9.26.7 (VO), JP2.1
unnamed: 9.14.3 (CA), R9.2
unnamed: 9.24.7 (VO), JP1.1
unnamed: 9.16.3 (CA), R10.2
unnamed: 9.18.3 (CA), R11.2
unnamed: C18.1, TPS73133.4 (NC/FB)
unnamed: 9.27.3 (CA), R12.2
unnamed: 9.41.3 (CA), R13.2
unnamed: 0000.3 (CA), R14.2
unnamed: 1111.3 (CA), R15.2
unnamed: 0000.5 (GND), 0000.6 (EN), C14.2, JP4.1, R16.1
unnamed: 1111.5 (GND), 1111.6 (EN), C15.2, JP48.1, R17.1
unnamed: 9.14.7 (VO), JP3.1
unnamed: 9.16.7 (VO), JP51.1
unnamed: 9.18.7 (VO), JP52.1
unnamed: 9.27.7 (VO), JP53.1
unnamed: 9.41.7 (VO), JP54.1
unnamed: 0000.8 (VCC), C14.1, JP47.1
unnamed: 1111.8 (VCC), C15.1, JP50.1
unnamed: 1111.7 (VO), JP49.1, R17.2
unnamed: 0000.7 (VO), JP46.1, R16.2
unnamed: 8.12.7 (VO), JP38.1
unnamed: 8.13.7 (VO), JP39.1
unnamed: 8.14.7 (VO), JP40.1
unnamed: 8.15.7 (VO), JP41.1
unnamed: 8.19.7 (VO), JP42.1
unnamed: 8.26.7 (VO), JP43.1
unnamed: U$2.45 (45_LCD_DATA0), U$3.P$19 (19-D18)
unnamed: U$2.46 (46_LCD_DATA1), U$3.P$20 (20-D19)
unnamed: U$2.43 (43_LCD_DATA2), U$3.P$22 (22-D20)
unnamed: U$2.44 (44_LCD_DATA3), U$3.P$23 (23-D21)
unnamed: U$2.41 (41_LCD_DATA4), U$3.P$24 (24-D22)
unnamed: U$2.42 (42_LCD_DATA5), U$3.P$4 (4-D7)
unnamed: U$2.39 (39_LCD_DATA6), U$3.P$6 (6-D8)
unnamed: U$2.40 (40_LCD_DATA7), U$3.P$7 (7-D9)
unnamed: U$2.37 (37_LCD_DATA8), U$3.P$11 (11-D12)
unnamed: U$2.38 (38_LCD_DATA9), U$3.P$12 (12-D13)
unnamed: U$2.36 (36_LCD_DATA10), U$3.P$14 (14-D14)
unnamed: U$2.34 (34_LCD_DATA11), U$3.P$52 (52-D1)
unnamed: U$2.35 (35_LCD_DATA12), U$3.P$54 (54-D2)
unnamed: U$2.33 (33_LCD_DATA13), U$3.P$55 (55-D3)
unnamed: U$2.31 (31_LCD_DATA14), U$3.P$56 (56-D4)
unnamed: U$2.32 (32_LCD_DATA15), U$3.P$3 (3-D6)
unnamed: U$3.P$2 (2-D5), U$19.P$1
unnamed: U$3.P$50 (50-D27), U$20.P$1
unnamed: U$3.P$8 (8-D10), U$21.P$1
unnamed: U$3.P$10 (10-D11), U$22.P$1
unnamed: U$3.P$16 (16-D16), U$23.P$1
unnamed: U$3.P$18 (18-D17), U$24.P$1
unnamed: U$3.P$25 (25-D23), U$25.P$1
unnamed: JP12.1, SPICS1.4 (+)
unnamed: U$3.P$48 (48-Y0M), U$4.1
unnamed: U$3.P$47 (47-Y0P), U$4.2
unnamed: U$3.P$46 (46-Y1M), U$4.3
unnamed: U$3.P$45 (45-Y1P), U$4.4
unnamed: U$3.P$42 (42-Y2M), U$4.5
unnamed: U$3.P$41 (41-Y2P), U$4.6
unnamed: U$3.P$40 (40-CLKOUTM), U$4.7
unnamed: U$3.P$39 (39-CLKOUTP), U$4.8
unnamed: U$3.P$38 (38-Y3M), U$4.9
unnamed: U$3.P$37 (37-Y3P), U$4.10
unnamed: JP21.1, U$15.1 (A)
unnamed: R19.1, U$6.2 (C)
unnamed: U$3.P$51 (51-D0), U$32.P$1
unnamed: U$3.P$15 (15-D15), U$33.P$1
unnamed: JP13.1, SPICS1.3 (-)
unnamed: JP14.1, SPICS3.4 (+)
unnamed: JP15.1, SPICS3.3 (-)
unnamed: C16.1, C25.1, TPS73133.1 (IN), TPS73133.3 (EN), U$2.51 (5_VDD_5V), U$2.52 (6_VDD_5V), U$16.P$1, U$18.3 (IN)
unnamed: R21.1, U$7.2 (C)
unnamed: R23.1, U$8.2 (C)
unnamed: R25.1, U$9.2 (C)
unnamed: R45.2, SPICS4.2 (C)
unnamed: R27.1, U$10.2 (C)
unnamed: R29.1, U$11.2 (C)
unnamed: R31.1, U$12.2 (C)
unnamed: JP16.1, SPICS2.4 (+)
unnamed: R33.1, U$13.2 (C)
unnamed: R35.1, U$14.2 (C)
unnamed: R37.1, U$15.2 (C)
unnamed: 9.3.3 (CA), R38.2
unnamed: R40.2, SPICS1.2 (C)
unnamed: R41.2, SPICS2.2 (C)
unnamed: LED1.K (C), R42.2
unnamed: 9.3.7 (VO), JP6.2
unnamed: 9.3.5 (GND), 9.3.6 (EN), C19.2, JP6.1
unnamed: JP5.1, U$6.1 (A)
unnamed: JP7.1, R19.2
unnamed: R43.1, U$1.2 (C)
unnamed: JP8.1, U$1.1 (A)
unnamed: JP9.1, R43.2
unnamed: 9.3.8 (VCC), C19.1, JP6.3
unnamed: R44.2, SPICS3.2 (C)
unnamed: JP17.1, SPICS2.3 (-)
unnamed: JP19.1, SPICS4.3 (-)
unnamed: JP18.1, SPICS4.4 (+)
unnamed: JP20.1, R37.2
unnamed: JP36.1, R35.2
unnamed: JP37.1, U$14.1 (A)
unnamed: JP34.1, R23.2
unnamed: JP35.1, U$8.1 (A)
unnamed: JP32.1, R21.2
unnamed: JP33.1, U$7.1 (A)
unnamed: JP30.1, R29.2
unnamed: JP31.1, U$11.1 (A)
unnamed: JP28.1, R27.2
unnamed: JP29.1, U$10.1 (A)
unnamed: JP26.1, R33.2
unnamed: JP27.1, U$13.1 (A)
unnamed: JP24.1, R31.2
unnamed: JP25.1, U$12.1 (A)
unnamed: JP22.1, R25.2
unnamed: JP23.1, U$9.1 (A)
PCLK: U$2.28 (28_LCD_PCLK), U$3.P$31 (31-CLKIN)
V-: 8.12.5 (GND), 8.12.6 (EN), 8.13.5 (GND), 8.13.6 (EN), 8.14.5 (GND), 8.14.6 (EN), 8.15.5 (GND), 8.15.6 (EN), 8.19.5 (GND), 8.19.6 (EN), 8.26.5 (GND), 8.26.6 (EN), C8.2, C9.2, C10.2, C11.2, C12.2, C13.2, JP45.1
VCC/2: C17.1, C20.1, C21.1, C22.1, TPS73133.5 (OUT), U$3.P$1 (1-IOVCC), U$3.P$9 (9-VCC), U$3.P$17 (17-CLKSEL), U$3.P$26 (26-IOVCC), U$3.P$30 (30-D26), U$3.P$34 (34-PLLVCC), U$3.P$44 (44-LVDSVCC)
VSYNC: U$2.27 (27_LCD_VSYNC), U$3.P$28 (28-D25)
XXXXXX: 9.14.8 (VCC), 9.16.8 (VCC), 9.18.8 (VCC), 9.24.8 (VCC), 9.26.8 (VCC), 9.27.8 (VCC), 9.41.8 (VCC), C1.1, C2.1, C3.1, C4.1, C5.1, C6.1, C7.1, JP55.1

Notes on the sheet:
PULL DOWN R FOR FAST BRAKE DURING ESTOP.
UART4 TX
UART4 RX
min 10uf

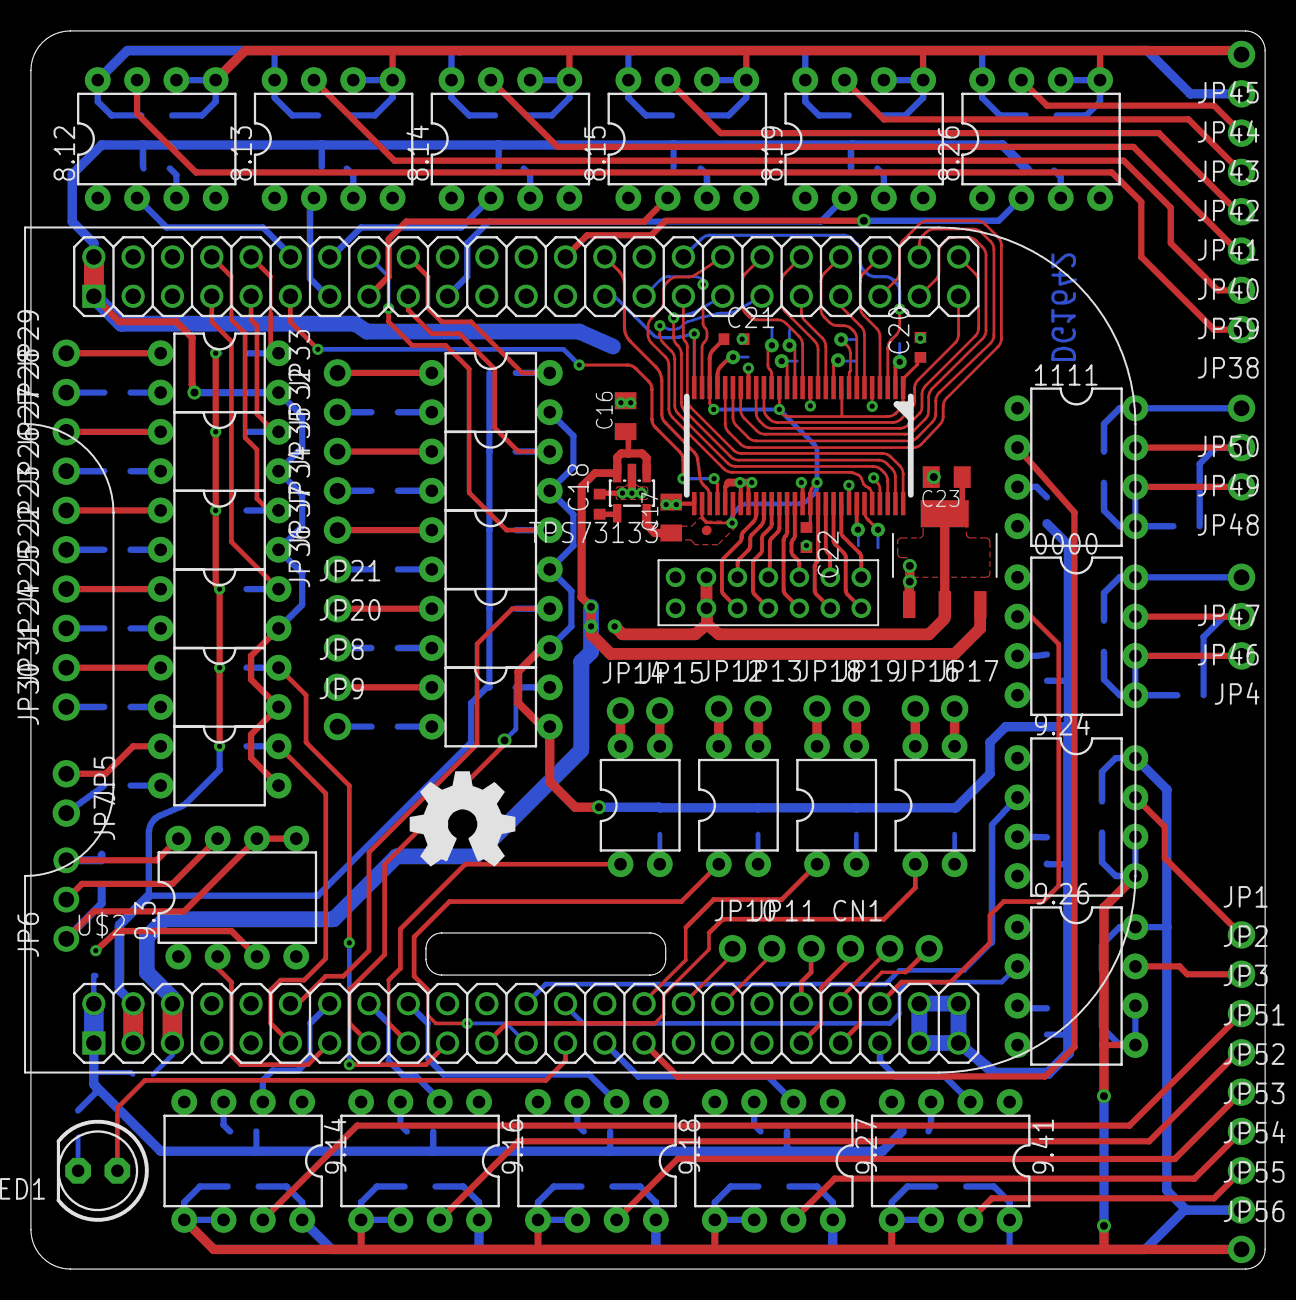
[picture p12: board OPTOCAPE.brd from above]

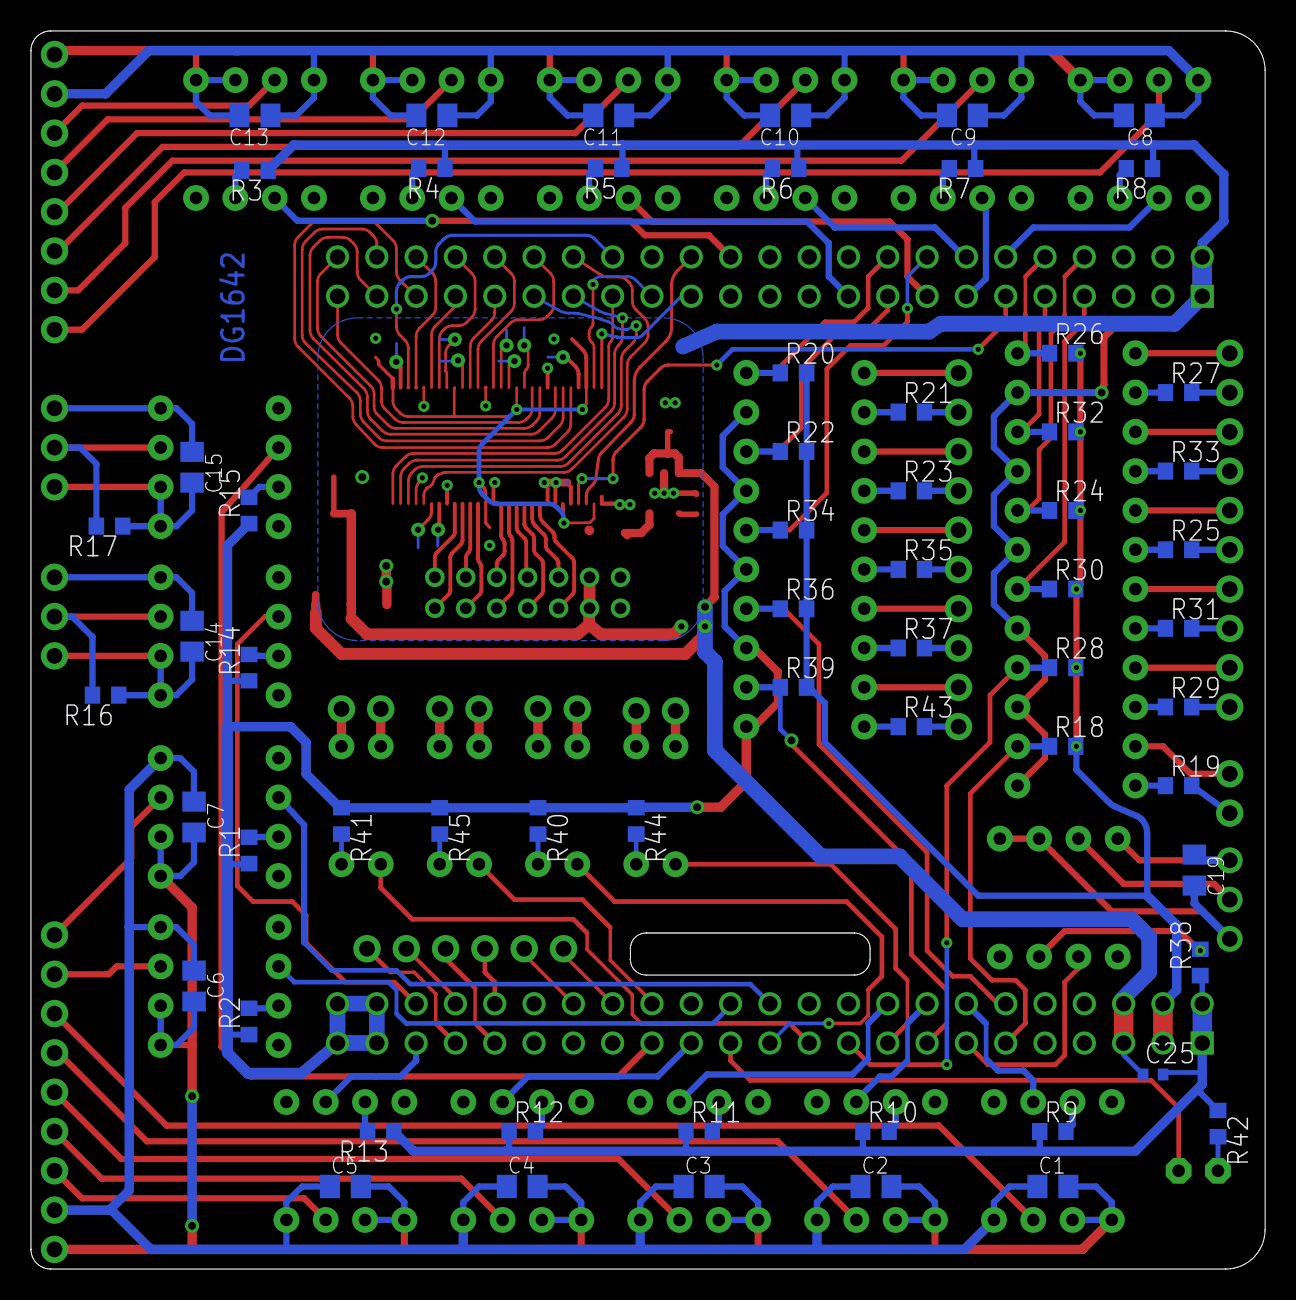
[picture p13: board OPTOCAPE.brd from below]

Board: 2 copper layers, 79.8 x 80.0 mm, 175 parts (62 on the bottom side), 171 nets.

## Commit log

2016-10-15 work in progress
    [CNC_IO_Buffer_Cape.brd, CNC_IO_Buffer_Cape.sch]
2016-10-19 V0.1 Fab version, not yet tested
    [OPTOCAPE.brd, OPTOCAPE.sch]
2017-03-27 removed UART4 from overlay
2017-04-06 added switch panel controller 0.1
    [SPC_1.GBL, SPC_1.GBS, SPC_1.GKO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]
2017-10-26 Optocape / BBB Pins compatability spreadsheet
    BBB_Pins spreadsheet www.embedded-things.com including a column for Optocape compatability
    [BBB_Pins_Optocape.xlsx]
2018-03-22 Shows a typical cable diagram for LCD display LVDS
